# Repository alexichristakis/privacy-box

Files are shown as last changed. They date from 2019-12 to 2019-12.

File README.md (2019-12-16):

# Behind Every Tap

A simple box with 7 eyes that look towards any side that is tapped. The enclosure is constructed out of laser-cut plywood, 3D printed mounting brackets, and wood glue. All fabrication files can be found under the fabrication folder.

## Artist Statement

Although we’re aware of how compromised our digital privacy is, it’s unclear where the digital and physical divide exists. Data collected from online and other digital activities have far reaching physical consequences, especially with the advent of IOT devices. Where we travel, what we do, eat, buy--even the smallest bits of data in aggregate threaten our privacy. By using the most abstract representation of an eye this project simulates the feeling of being watched. Even the smallest disturbance to a side of the box triggers an immediate response.

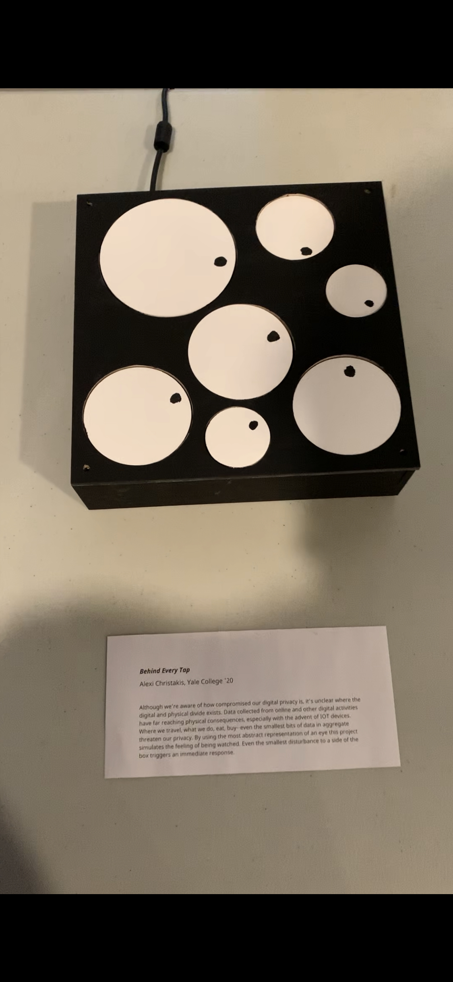
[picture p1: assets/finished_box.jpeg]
Finished box


## Materials List

### Electronics

7 180deg micro-servos (~$28)

1 MPU6050 accelerometer (~$20)

1 ESP32 (~$20)

1 10amp 5v power brick (~15)

1 power switch (<$1)

#### Total: ~$85

### Enclosure

1 24in x 24in sheet of 0.24in thick plywood (~$7)

7x3 male headers for the servos

2x16 male headers for an ESP mount

wood glue

jumper wires, solder

various screws, and nuts to secure the box

black & white acrylic paint

access to laser cutter

access Makerbot 3D printer

## Fabrication

Because readily-available positionally-aware servos have a limited range of 180 degrees, the layout had to carefully consider the angle of each mounted servo to enable them to look at all 4 sides of the box. In the layout shown below, every servo has its available range directed towards the center of the box, with two extremes positioned at two adjacent sides.

While the original plan involved using either piezoelectric or vibration sensors to detect which side of the box the user tapped, it ultimately was too difficult to differentiate between the sensor's signals to determine which side was activated. Using an accelerometer, the box listens to it's horizontal and vertical acceleration to detect if it was tapped. One issue with this solution is that the deceleration of the box can outweigh the initial acceleration, leading to the code misreading the data as a tap from the opposite side.

### Layout

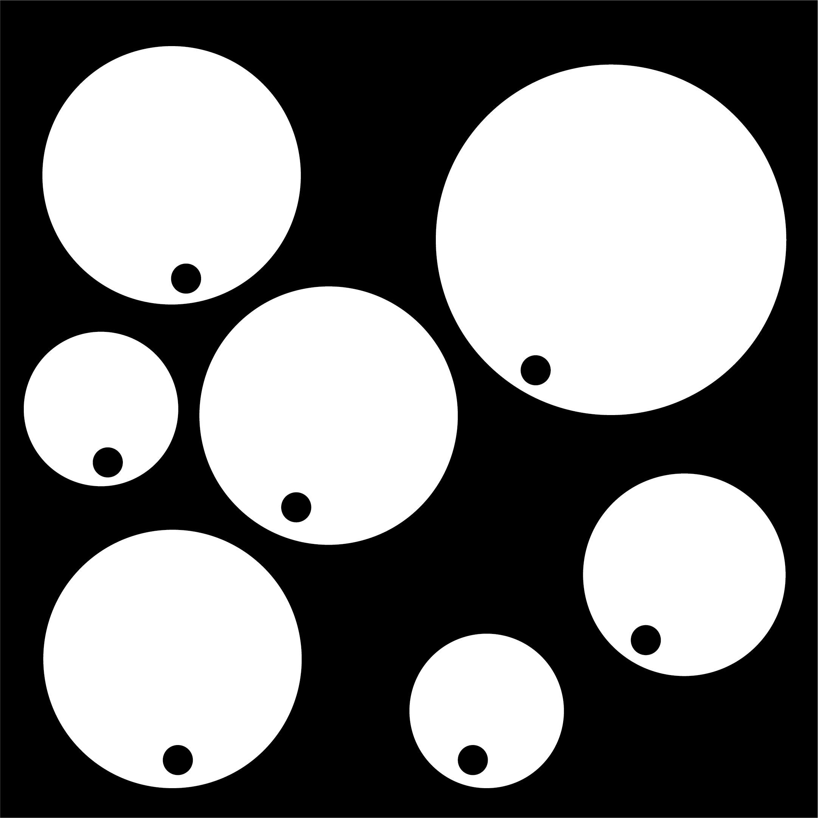
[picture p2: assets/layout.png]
Box layout


### Wiring

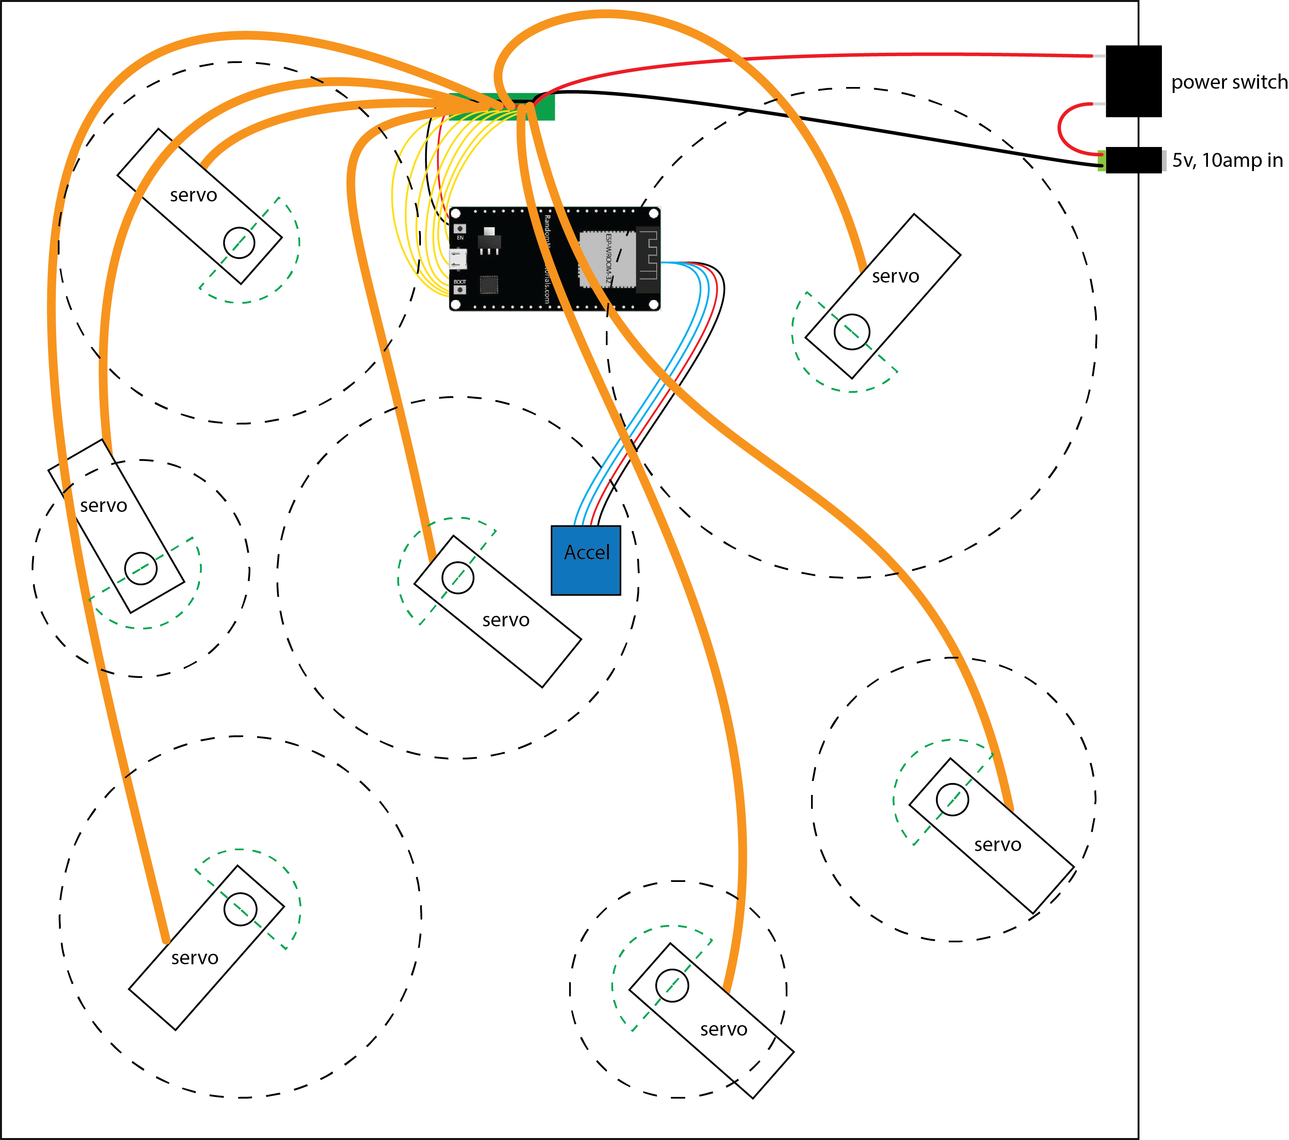
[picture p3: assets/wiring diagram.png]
Wiring diagram


The wiring diagram shows each mounted servo with a dashed circle representing the size and position of the eye it controls, as well as a dashed semi-circle depicting the available rotation. The 7 servos are connected to the ESP's pins 12, 13, 14, 25, 26, 27, and 33 for PWM position control. The accelerometer is powered from the 5V pin, and uses pins 2 and 15 for digital data transfer with help from the Wire library.

Power comes from a converter supplying 10 amps at 5 volts to a daughter-board which powers each servo and the ESP in parallel. 7 sets of 3 pin male headers are connected to the rail, with the signal pins connected to the ESP.

Here's an picture from the box's construction where vibration sensors were still being used:

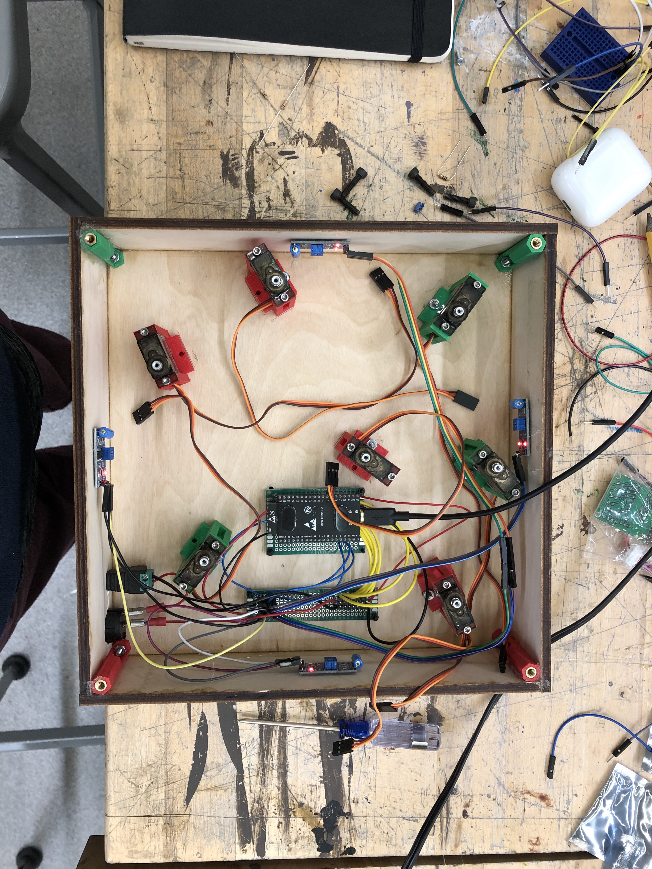
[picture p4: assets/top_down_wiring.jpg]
Open wiring


The servo mounts which secure the motors to the bottom plate of the box were designed in SketchUp and look like this:

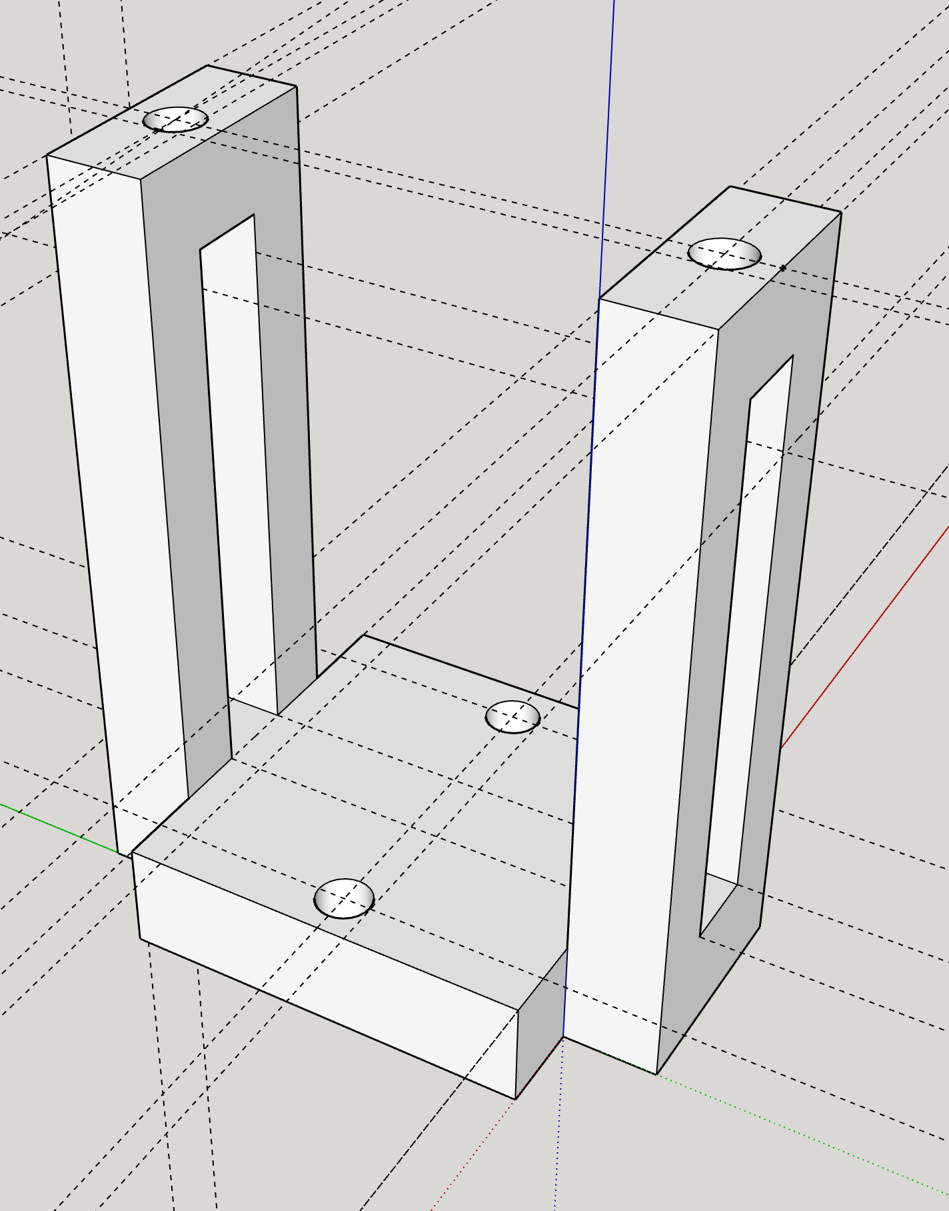
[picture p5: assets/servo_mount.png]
Servo mount


Four connector pieces were also printed to secure the lid to the box in a removable way. They hold a nut in each side to make the construction easier.

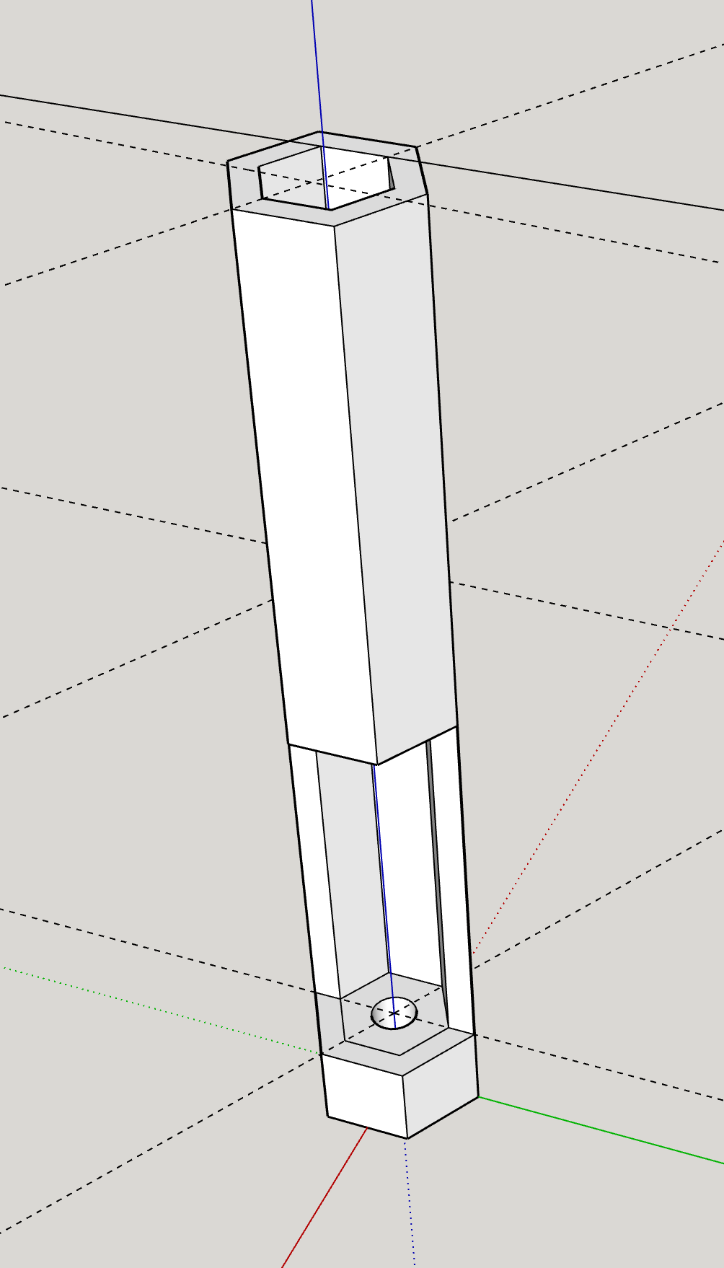
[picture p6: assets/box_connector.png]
Connector


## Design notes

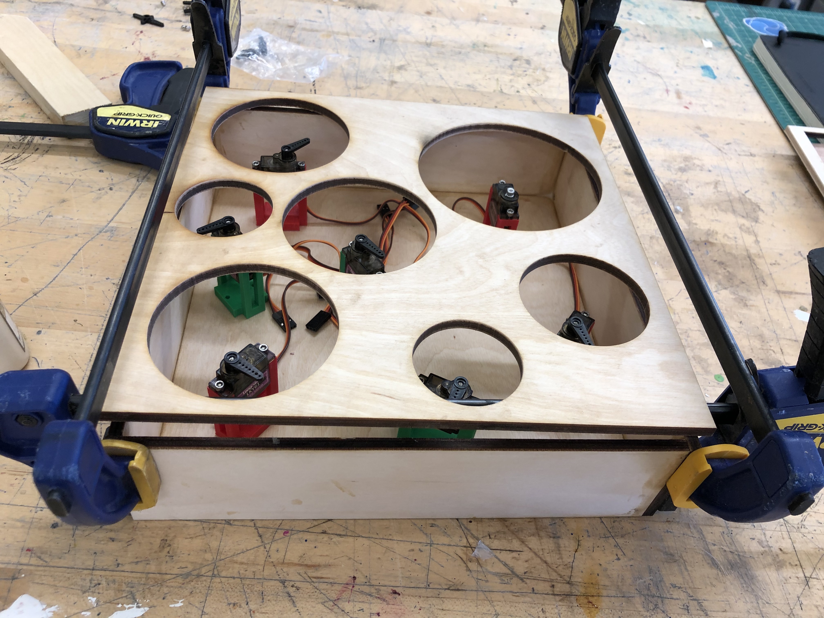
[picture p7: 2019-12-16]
assets/clamped_box.jpg

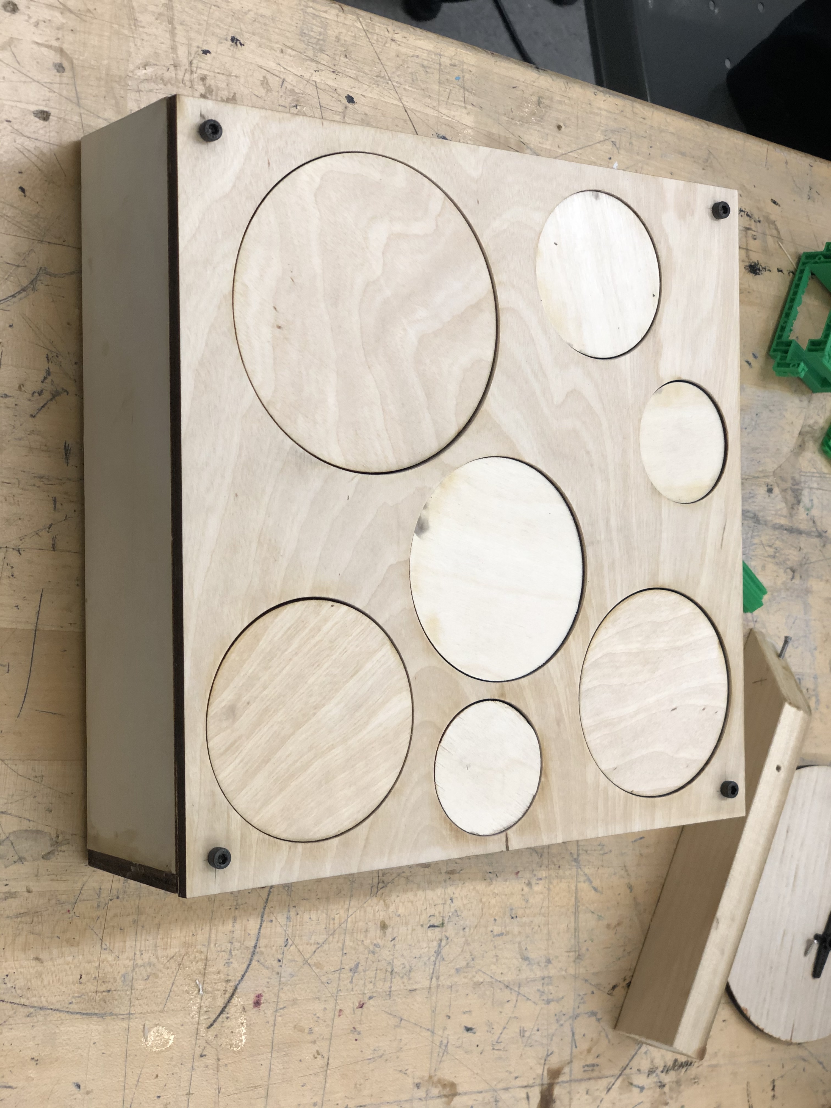
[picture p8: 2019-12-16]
assets/box_sealed.jpg

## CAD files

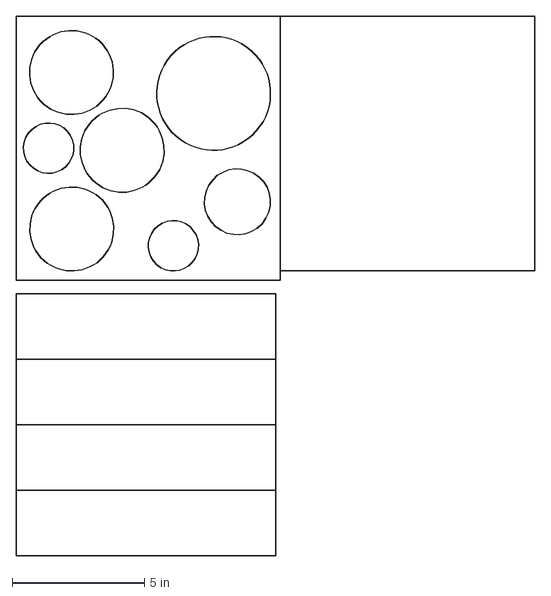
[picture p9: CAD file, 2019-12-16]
fabrication/layout.dxf
19.6 x 20.4 in

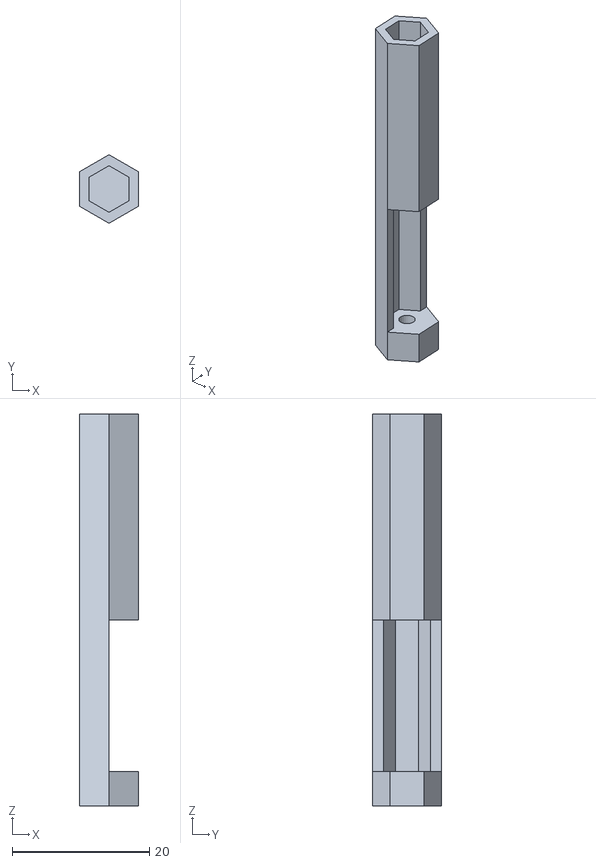
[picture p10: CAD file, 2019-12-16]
fabrication/box_connector.stl
8.66 x 10.0 x 57.2

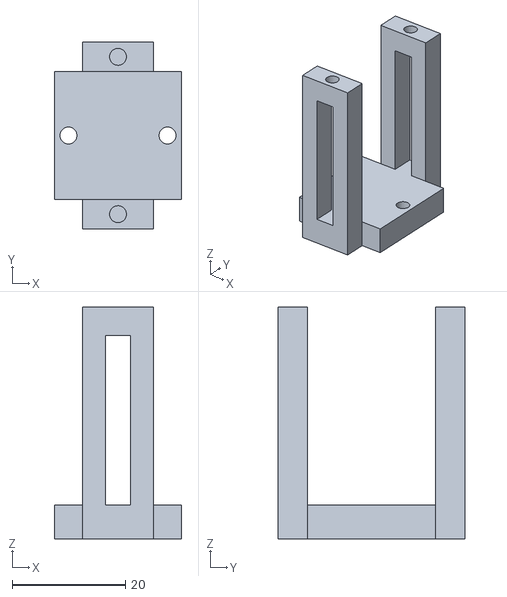
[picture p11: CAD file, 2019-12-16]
fabrication/servo_mount.stl
22.5 x 33.0 x 41.0

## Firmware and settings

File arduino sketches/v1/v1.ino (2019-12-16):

#include <ESP32_Servo.h>
#include <MPU6050_tockn.h>
#include <Wire.h>

const int NUM_SIDES = 4;
const int NUM_SERVOS = 7;

// the servos
Servo servos[NUM_SERVOS];
MPU6050 mpu6050(Wire);

// pins for the servo PWM
int servoPins[]  = { 13, 14, 25, 26, 27, 12, 33 };

// mapping of servo index to the positions it takes for each
// side of the box
const int sidePositions[][NUM_SIDES]  = {
  { 1305, 1800, 2505, 5 }, // check key for which servo
  { 2505, 5, 1000, 1700 }, // T, L, B, R (index => side mapping, where top has power in)
  { 2005, 2600, 5, 1100 },
  { 1800, 2500, 5, 1400 },
  { 5, 1600, 2200, 2600 },
  { 5, 1100, 1600, 2600 },
  { 1950, 2600, 5, 1400 },
};

// intial servo positions
int servoPositions[] = { 5, 5, 5, 5, 5, 5, 5 };

int activatedSide = 0;

// calibration for accelerometer
float calibration[] = { 0, 0 };

const int MIN_MICRO = 5;
const int MAX_MICRO = 2600;

void setup() {
  for (int i = 0; i < NUM_SERVOS; i++) {
    servos[i].attach(servoPins[i], MIN_MICRO, MAX_MICRO);
  }

  Wire.begin(2, 15);
  mpu6050.begin();

  calibration[0] = mpu6050.getAccX();
  calibration[1] = mpu6050.getAccY();
  
  Serial.begin(115200);
}

// sweep a servo through it's range
void sweepServo(int servo) {
   for (int pos = MIN_MICRO; pos <= MAX_MICRO; pos += 100) {
    servos[servo].writeMicroseconds(pos);
    Serial.println(pos);
    delay(500);
  }
}

// for calibrating positions of each servo
void rangeServo(int servo) {
   for (int side = 0; side < 4; side++) {
      servos[servo].writeMicroseconds(positions[servo][side]);
      Serial.print(side);
      Serial.print(", ");
      Serial.print(positions[servo][side]);
      Serial.print(", ");
      delay(500);
  }
  Serial.println();
}

void updateServos() {
  for (int servo = 0; servo < NUM_SERVOS; servo++) {
    servos[servo].writeMicroseconds(servoPositions[servo]);
  }
}

void randomStep(int servo) {
  int currentPosition = positions[servo];

  if (random() > 0.5) {
    // take a step
    int stepSize = (random() - 0.5) * 100;
    int newPosition = currentPosition + stepSize;
    
    positions[servo] = newPosition;
  }
}


void randomWalk() {
  for (int servo = 0; servo < NUM_SERVOS; servo++) {
    randomStep(servo);
  }
}

void writePositions(int side) {
  for (int servo = 0; servo < NUM_SERVOS; servo++) {
    servoPositions[servo] = positions[servo][side];
  }
}



void loop() {
  mpu6050.update();

  float accX = mpu6050.getAccX();
  float accY = mpu6050.getAccY();


  float diffX = accX - calibration[0];
  float diffY = accY - calibration[1];
  if (diffX * diffX > 0.1 || diffY * diffY > 0.1) {
    if (diffX > 0) activatedSide = 3;
    if (diffX < 0) activatedSide = 1;
    
    if (diffY > 0) activatedSide = 2;
    if (diffY < 0) activatedSide = 0;

    writePositions(activatedSide);
  } else {
    randomWalk();
  }
  
  updateServos();
  delay(200);
}

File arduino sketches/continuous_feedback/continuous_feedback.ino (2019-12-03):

#include <ESP32_Servo.h>


Servo servo;

int pos = 0;
int connectedState = 0;


void setup() {
  servo.attach(13);
  Serial.begin(115200);

  pinMode(23, INPUT);
  pinMode(4, INPUT);
 
//
}

void loop() {
  int val = digitalRead(23);
  int shouldMove = digitalRead(4);

  if (shouldMove) {
    servo.write(0);
  }

  if (val && !connectedState) {
    connectedState = 1;
    
    pos += 1;

    if (pos == 4) {
      pos = 0;
    }

    Serial.println(pos);
  }

  if (pos == 3) {
    servo.write(90);
  }

  if (!val) {
    connectedState = 0;
  }
  

  delay(500);
}

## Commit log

2019-12-03 initial stuff
    [servo mount 2.0.skp, servo mount.skp, small servo mount.skp]
2019-12-03 add other fabrication files
    [fritz.fzz]
2019-12-06 arduino code working
    [connector bracket.skp, connector bracket~.skp, small servo mount.skp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]
2019-12-16 more assets
    [box_connector.stl, connector bracket.skp, connector bracket~.skp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]
2019-12-16 add materials list
